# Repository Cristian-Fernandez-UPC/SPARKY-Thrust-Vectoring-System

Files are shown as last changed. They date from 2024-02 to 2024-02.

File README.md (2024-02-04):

# SPARKY Thrust Vectoring System
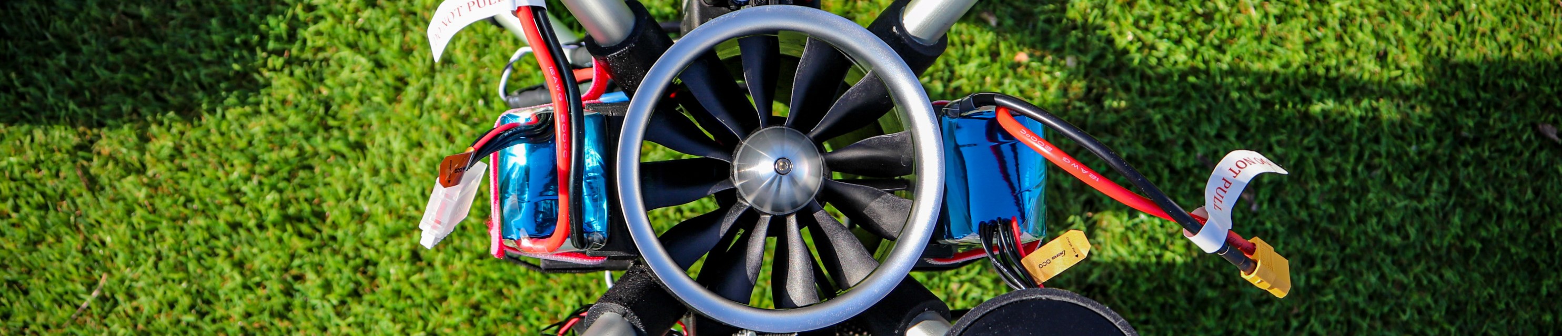
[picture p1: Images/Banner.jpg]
Banner

### Development and manufacturing of a Thrust Vectoring System for reusable rocket dynamics research - Final Bachelor's Thesis

Author: Cristian Fernandez Dominguez

Advisors: Pablo Royo Chic & Ramon Casanella Alonso

Bachelor’s degree in Aerospace Systems Engineering

Castelldefels School of Telecommunications and Aerospace Engineering

## :small_orange_diamond: Introduction
Nowadays, the space industry is experiencing exponential growth, fueled by private companies and the conception of new and ambitious challenges. In recent years, the cost of reaching space has been drastically reduced, and to a certain extent, reusable rockets are to blame for that cost reduction.

Unfortunately, and it has always been so, the space industry has always required a lot of resources and funding, and even with the drastic cost reduction with the incorporation of this new type of rockets, the development of technologies by students and researchers from universities around the world is still very difficult.

To address this problem, this thesis will attempt, by reducing the cost to a maximum, to develop a system where it can study the dynamics of reusable rockets and be able to develop technologies around them.

To do this, an unmanned aircraft system (UAS) will be designed from scratch with the main objective of imitating the behavior of this type of rocket while trying to reuse as many components already used by the university as possible, helping to reduce costs, and helping the sustainability of the project itself.

Through the different chapters of this work, it can be seen, from the conception of the initial requirements and selection of the components, to the 3D design and subsequent manufacturing of the system itself, which will be calibrated and tested in different test flights, taking advantage of the university's facilities.

## :small_orange_diamond: Media Overview
In this repository you can find all the files related of this final bachelor's thesis. Also the `Checklist` procedure and the `Connections Diagram` are in this repository. The files are organized as follows:

- [3D_Models](3D_Models) - This folder contains the `.stl` files for all components of Sparky. Utilizing these files, users with access to a suitable 3D printer can fabricate the individual parts and assemble them to create a functional UAS with VTOL capabilities.

- [3D_Sparky_Designs](3D_Sparky_Designs) - This folder gives access to the SolidWorks files of the different versions of Sparky and additionally to the Gimbal that works to calibrate the PIDs.

- [DataLogs](DataLogs) - This folder contains all the DataLogs in a `.bin` format of the different Flight Tests.

- [Images](Images) - Some cool images.

- [Parameters](Parameters) - This folder contains the different parameters used in the real flight tests in `.param` files.

In addition, a **YouTube channel** has been created to be able to upload the different videos of the test flights and a trailer that encompasses the entire project itself. The channel is [@CristianFernandezUPC](https://www.youtube.com/@CristianFernandezUPC/featured). 

The uploaded videos are:

- [Sparky Trailer](https://www.youtube.com/watch?v=5irSOpZRAP4)
- [Flight Test 1](https://www.youtube.com/watch?v=05G50puAUSE)
- [Flight Test 2](https://www.youtube.com/watch?v=WWrm3nAGPkM&t=1s)

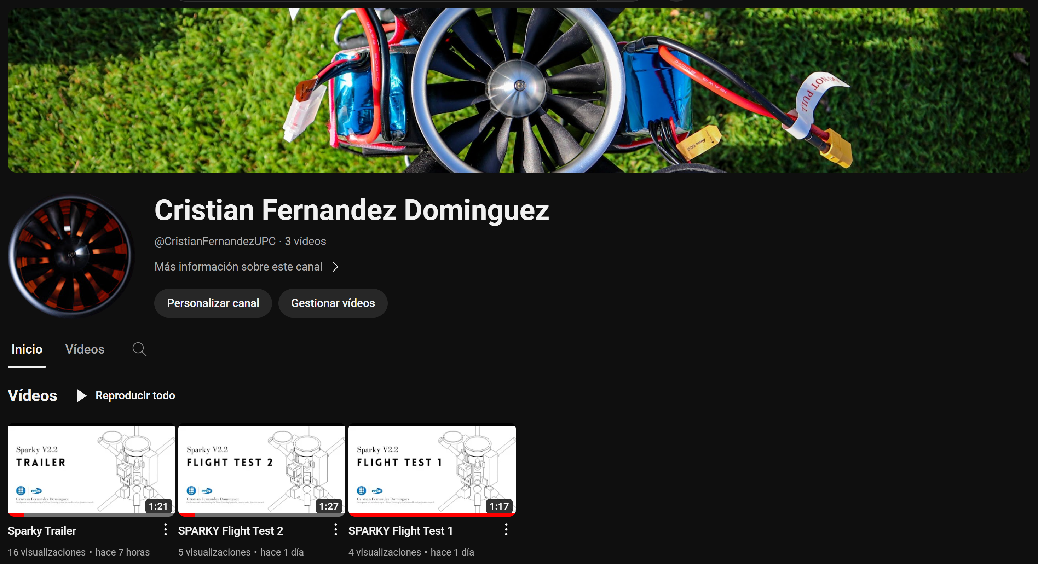
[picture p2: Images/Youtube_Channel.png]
ImgYoutube


## :small_orange_diamond: Components

- [Mini Set The Cube Orange+](https://rc-innovations.es/shop/pixhawk-2-1-mini-set-the-cube-orange-plus#attr=8269)

- [FrSky Taranis X9D PLUS](https://rc-innovations.es/shop/frsky-taranis-x9d-plus-se-2019-access-2-4ghz-carbono#attr=7182)

- [Here 3 + GPS Module](https://rc-innovations.es/shop/here-3-plus-modulo-gps-gnss-m8p-2-pixhawk-2-istand?search=here+3#attr=7478)

- [Gens ACE LiPo Battery 2500mAh (x2)](https://rc-innovations.es/shop/gens-ace-6s-22-2v-2500mah-80c-bateria-lipo?page=3&category=356#attr=8748,8749,8747)

- [KingMax Digital Servo (x4)](https://rc-innovations.es/shop/kingmax-km5514mdhv-20mm-59g-13kg-digital-metalico-coreless#attr=8001,7999,8000,8002)

- [HSD Jets EDF 90mm Brushless Motor](https://rc-innovations.es/shop/a58010000j-hsd-jets-s-edf-90mm-brushless-motor-10579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)

- [Hobbywing ESC 110A OPTO](https://rc-innovations.es/shop/esc-hobbywing-flyfun-hv-110a-v5-OPTO#attr=)

- [Holybro Telemetry Module V3](https://rc-innovations.es/shop/holybro-modulos-telemetria-sik-v3-433mhz-500mw?search=holybro+v3#attr=8351)

- [3DJake White Matte PLA 1000g (x2)](https://www.3djake.es/3djake/ecopla-mate-blanco)

- [Holybro PM02 V3 Power Module](https://rc-innovations.es/shop/modulo-alimentacion-pmu-holybro-pm02-v3-original-sensor-consumo-pmu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)

- [20mm Bearings](https://www.amazon.es/dp/B09VZGCW9H?ref=ppx_pop_dt_b_product_details&th=1)

- [Montana Paint Primer Plastics](https://www.amazon.es/dp/B0826FCM71?psc=1&ref=ppx_pop_dt_b_product_details)

- [Hobbywing UBEC 3A](https://rc-innovations.es/shop/Hobbywing-ubec-3a?search=ubec#attr=)

- [Anodized aluminum tube Ø16mm (1m) (x2)](https://www.fesmes.com/es/perfiles-de-aluminio/295205005-tubo-redondo-aluminio-anodizado-plata-8013237011109.html)

- [Montana Matte Black Paint](https://www.amazon.es/dp/B008UGFJU2?psc=1&ref=ppx_pop_dt_b_product_details)

- [Anodized Aluminum Square Tube 20mm x 20mm (1m)](https://www.fesmes.com/es/perfiles-de-aluminio/295204000-tubo-cuadrado-aluminio-anodizado-plata-8013237011925.html)

- [Anodized aluminum tube Ø20mm (1m)](https://www.fesmes.com/es/perfiles-de-aluminio/295205005-tubo-redondo-aluminio-anodizado-plata-8013237011109.html)

- [XT30 Connector (pair) (x3)](https://rc-innovations.es/shop/Amass-conector-xt30-pareja?search=xt30#attr=)

- [EC5 Connector (pair)](https://rc-innovations.es/shop/Hobbywing-ubec-3a?search=ubec#attr=)

## :small_orange_diamond: Project Images

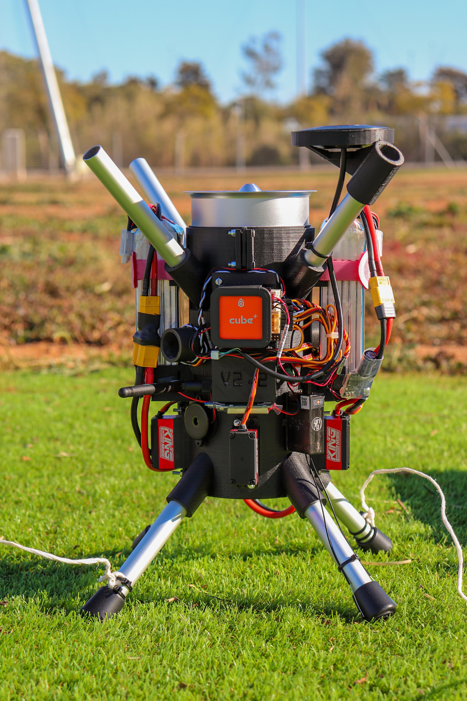
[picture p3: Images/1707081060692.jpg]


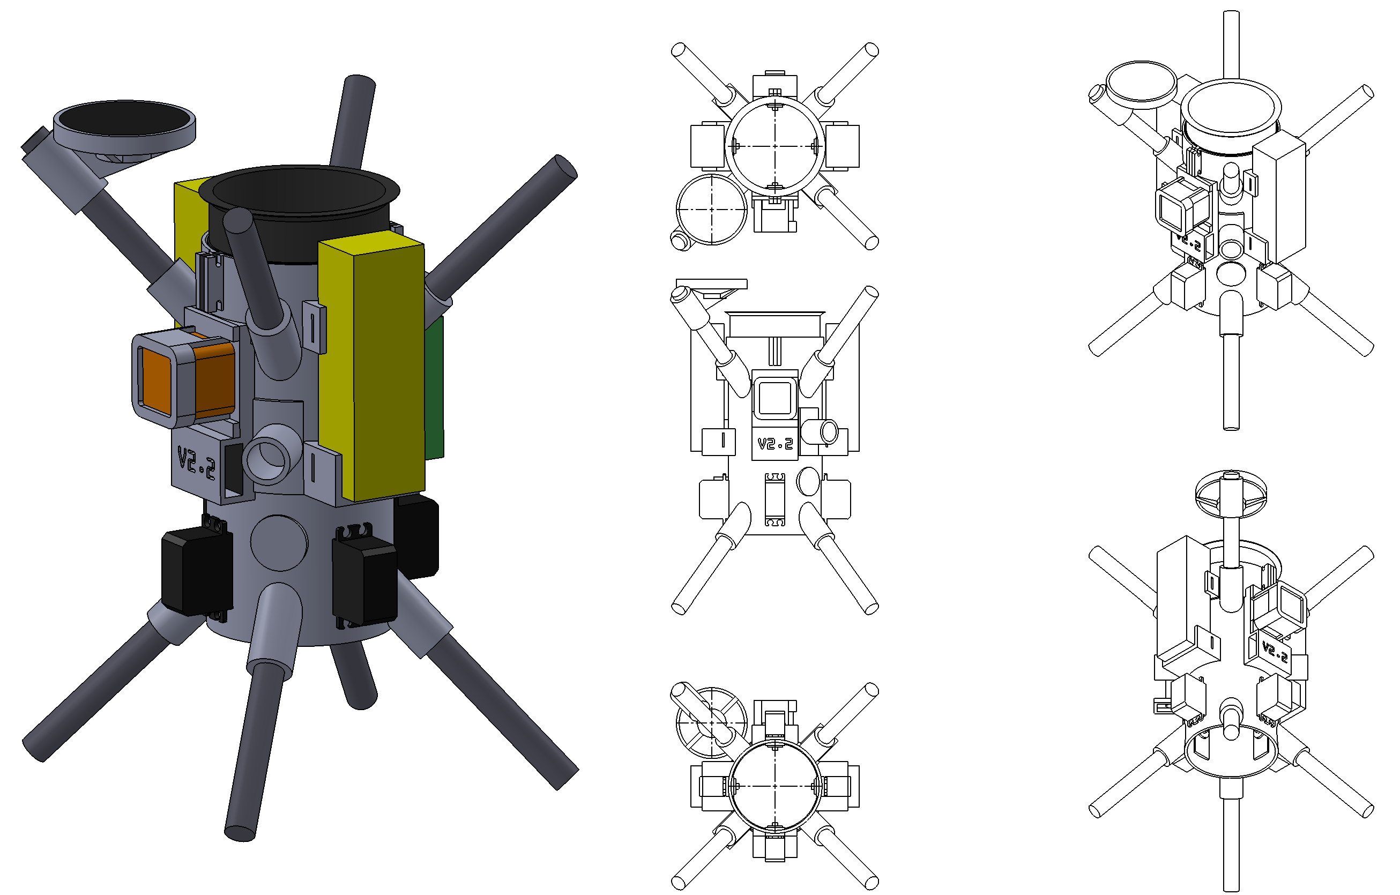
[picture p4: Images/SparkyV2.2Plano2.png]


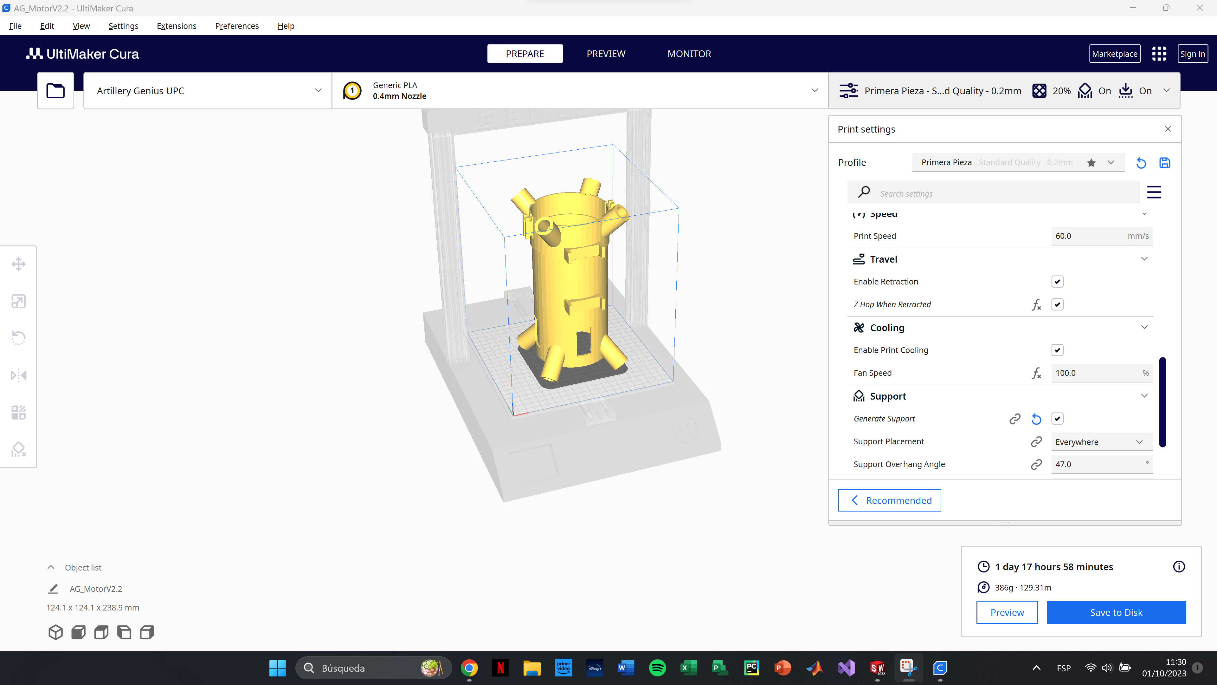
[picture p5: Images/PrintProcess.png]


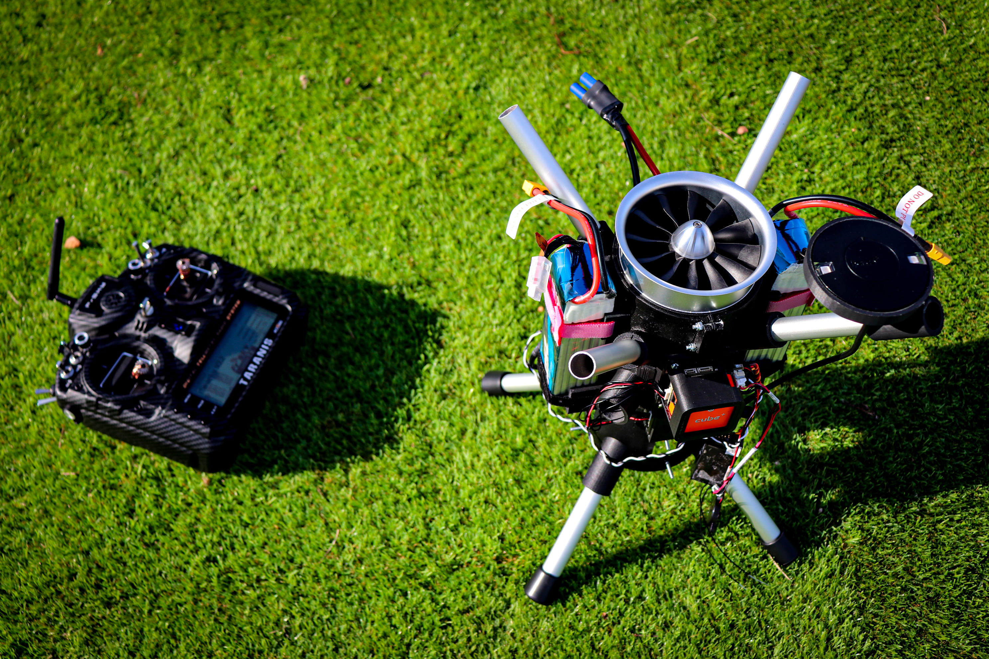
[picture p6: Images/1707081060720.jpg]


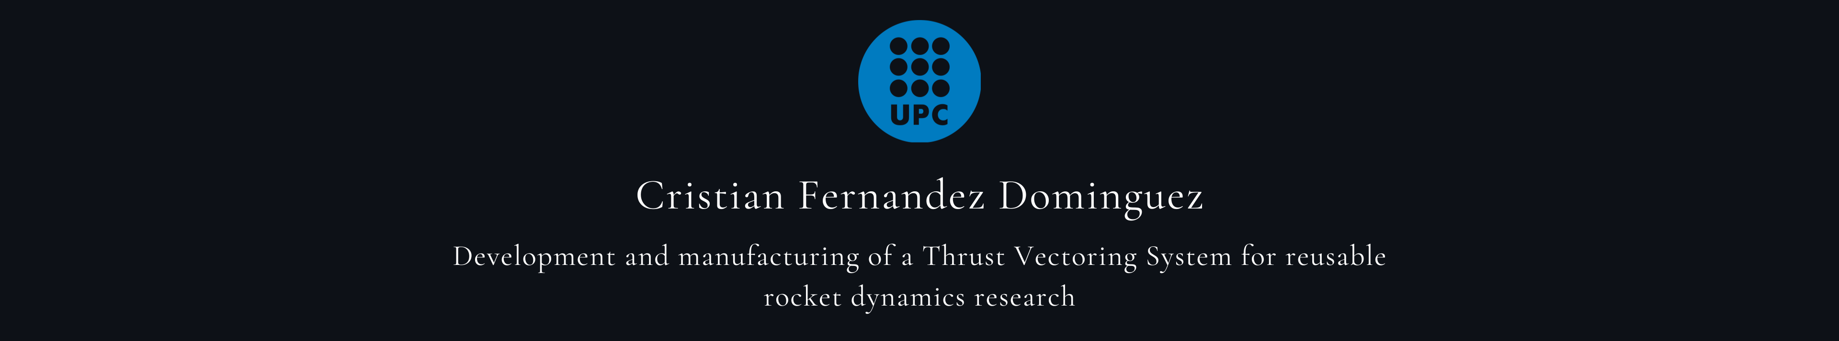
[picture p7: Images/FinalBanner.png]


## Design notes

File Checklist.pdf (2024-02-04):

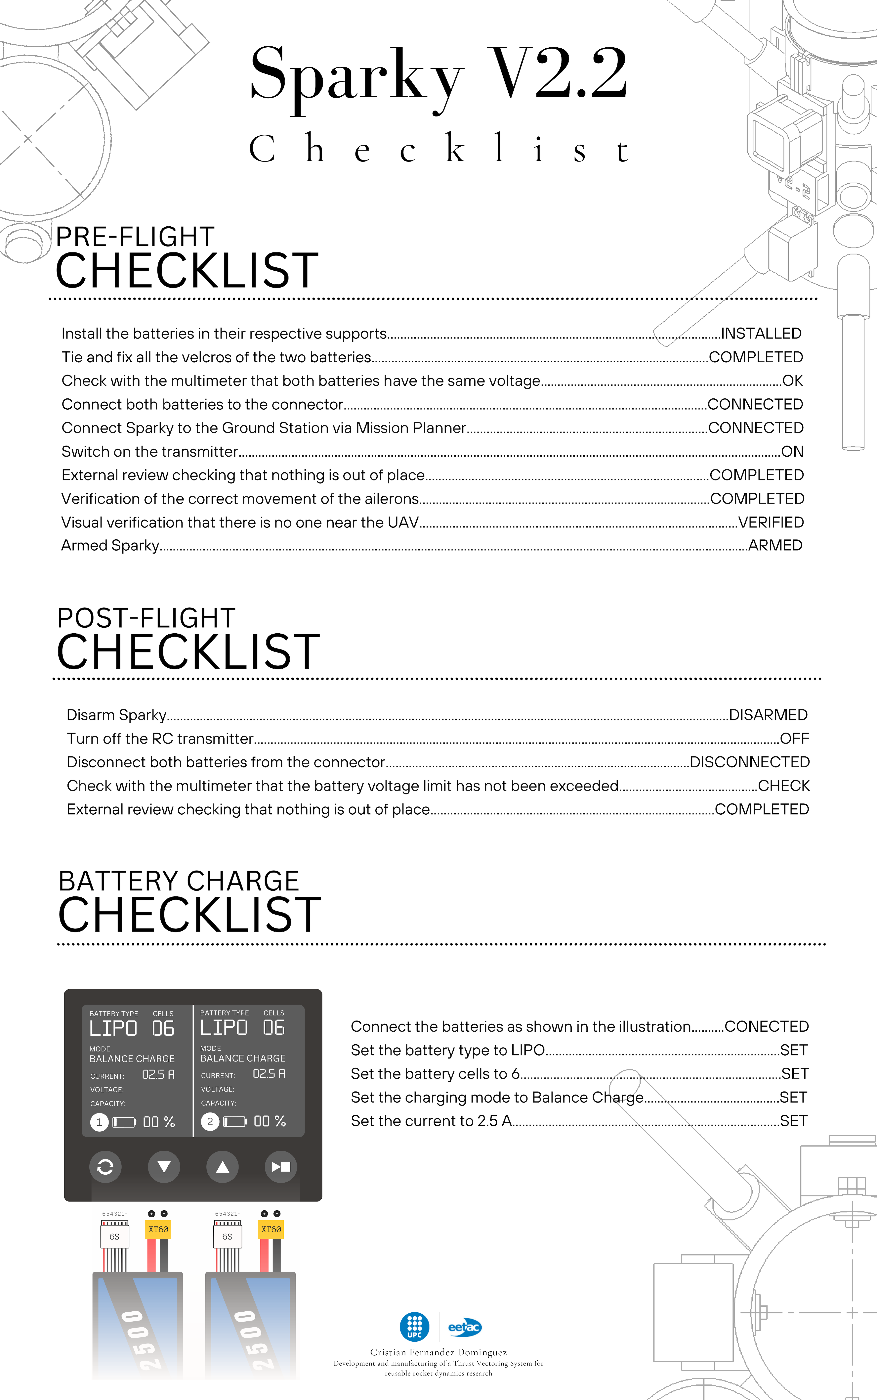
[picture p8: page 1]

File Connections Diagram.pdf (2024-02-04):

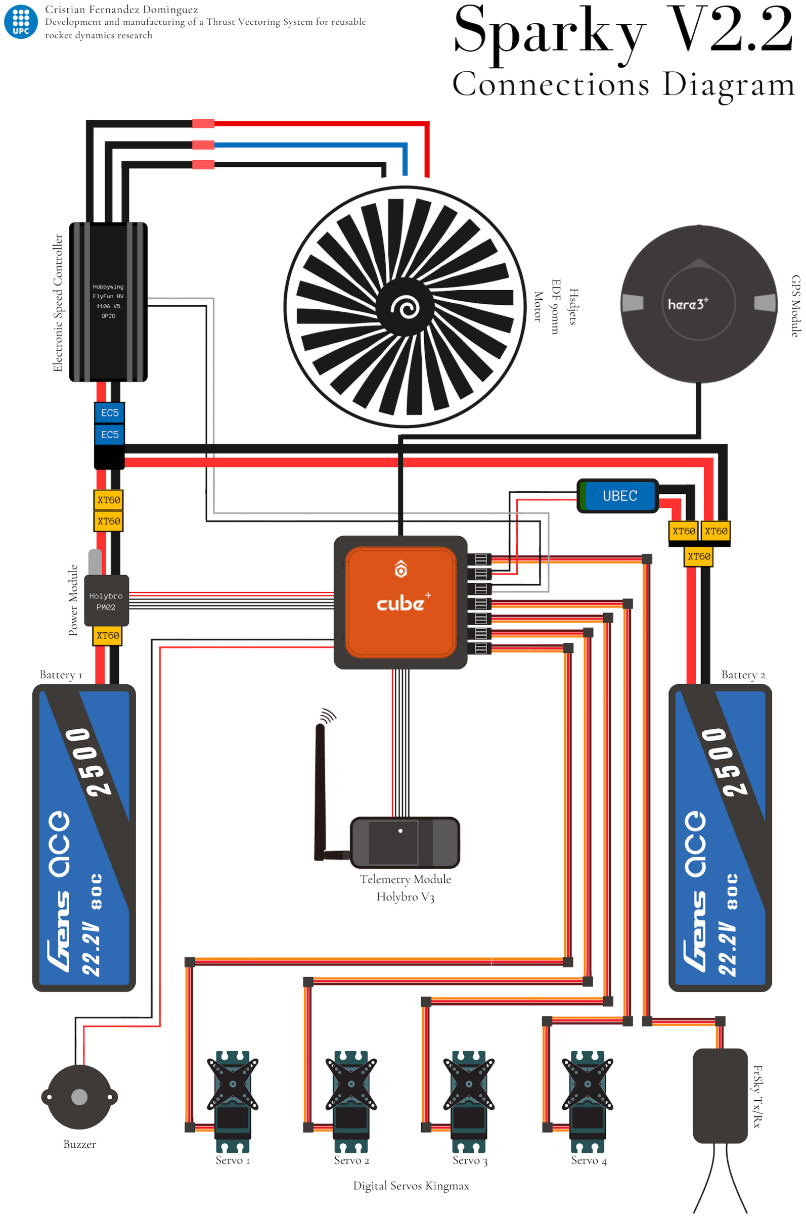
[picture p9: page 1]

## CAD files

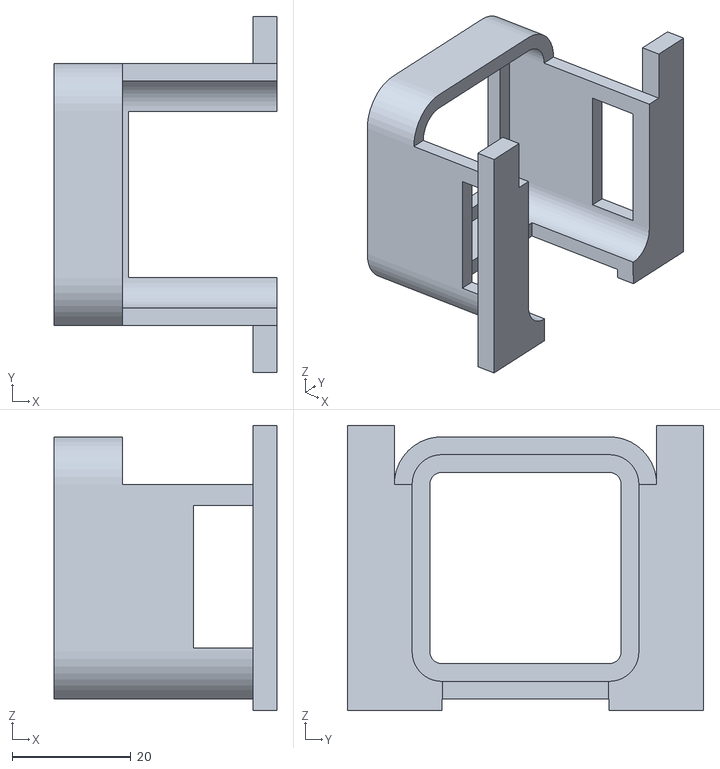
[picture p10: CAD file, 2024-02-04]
3D_Models/Cube 1_Support.STL
37.5 x 60.0 x 48.0

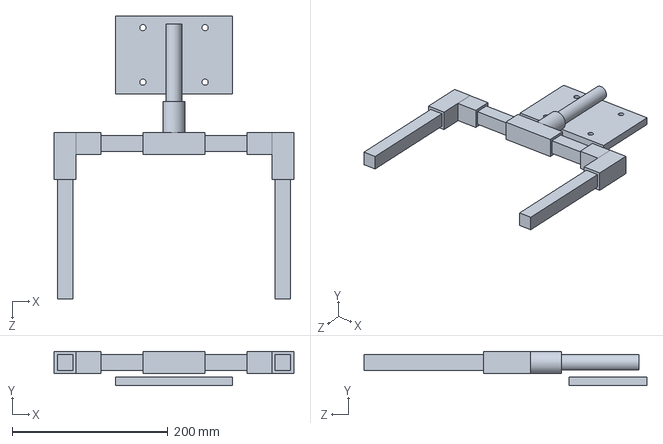
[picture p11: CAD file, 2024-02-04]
3D_Sparky_Designs/Gimbal_Support.SLDPRT
308.0 x 44.2 x 363.8 mm

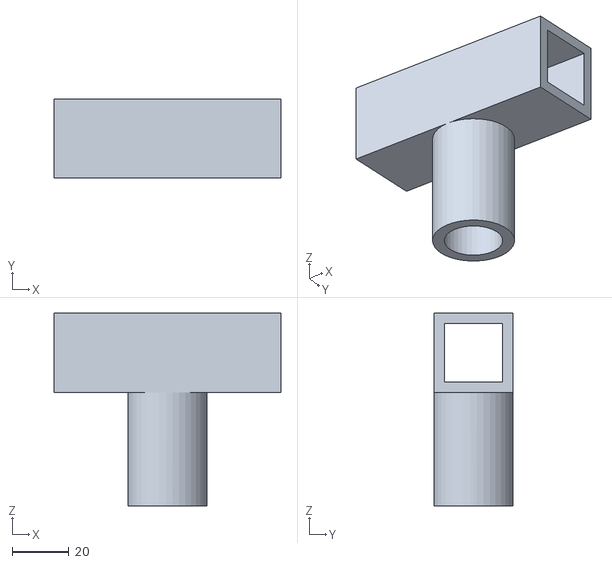
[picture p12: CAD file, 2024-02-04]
3D_Models/Gimbal_1_V2_Support.STL
80.0 x 28.0 x 68.0

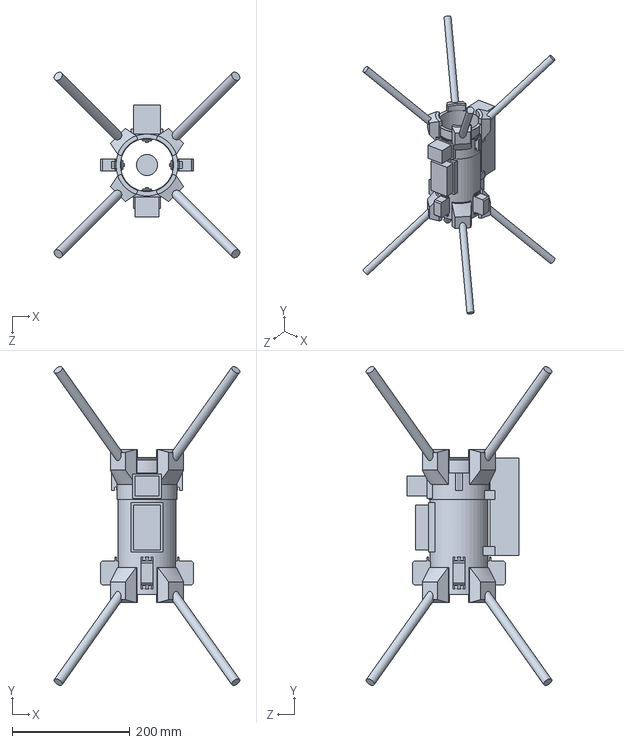
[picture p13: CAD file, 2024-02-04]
3D_Sparky_Designs/Sparky_V2.SLDPRT
315.1 x 541.1 x 315.1 mm

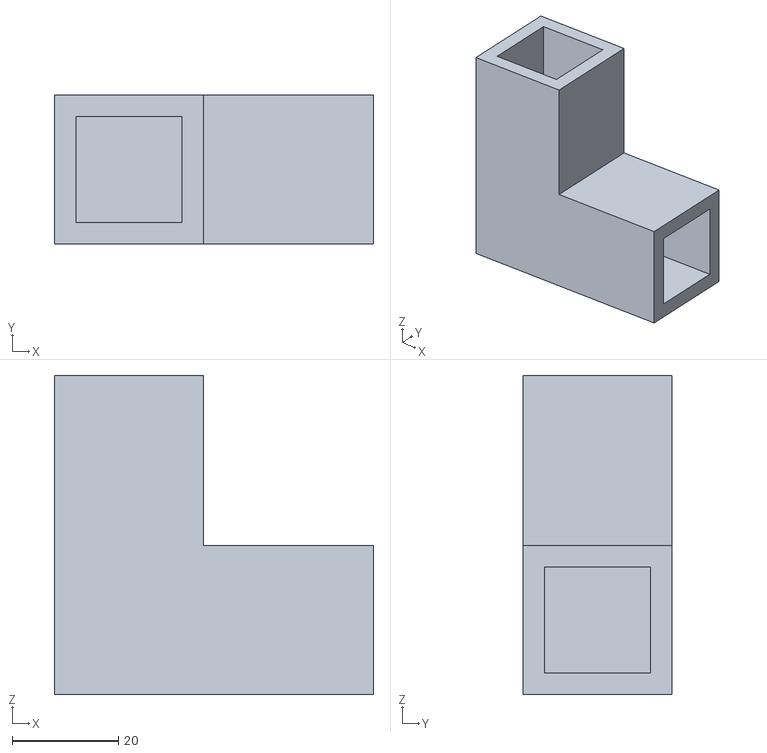
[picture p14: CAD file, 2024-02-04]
3D_Models/Gimbal_2_Support.STL
60.0 x 28.0 x 60.0

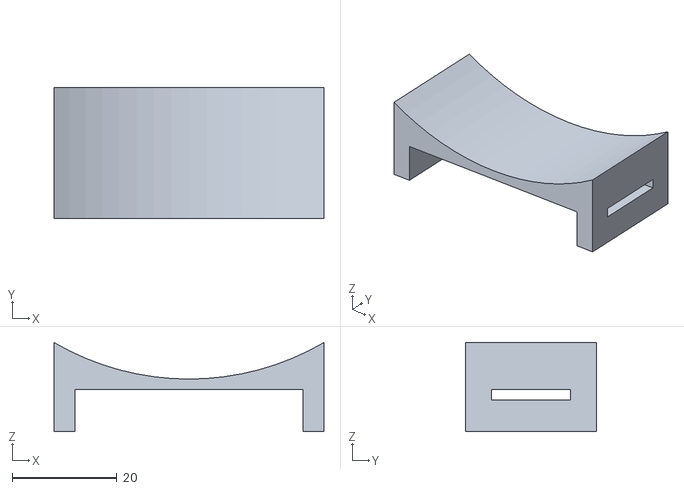
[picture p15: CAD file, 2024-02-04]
3D_Models/BAT_1_Support.STL
51.5 x 25.0 x 17.0

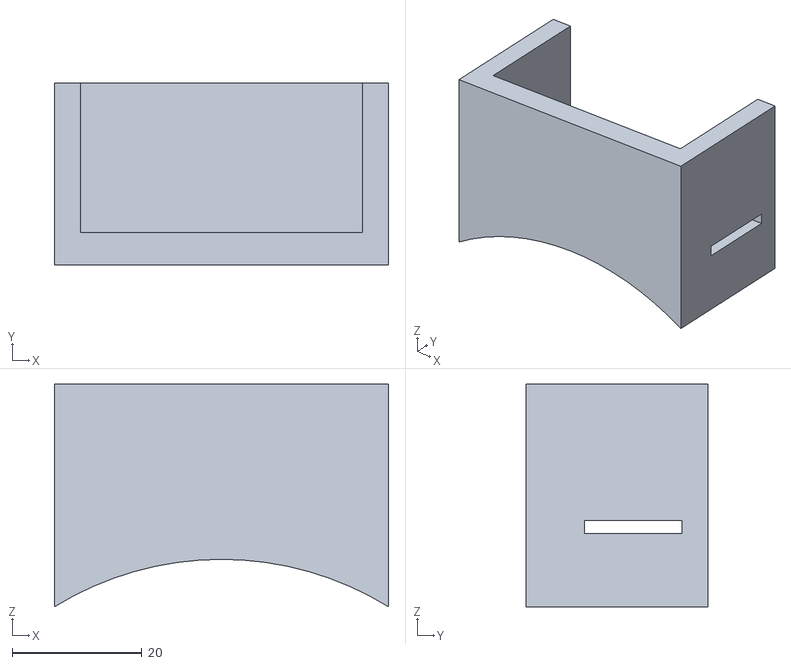
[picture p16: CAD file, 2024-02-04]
3D_Models/BAT_2_Support.STL
51.5 x 28.0 x 34.3

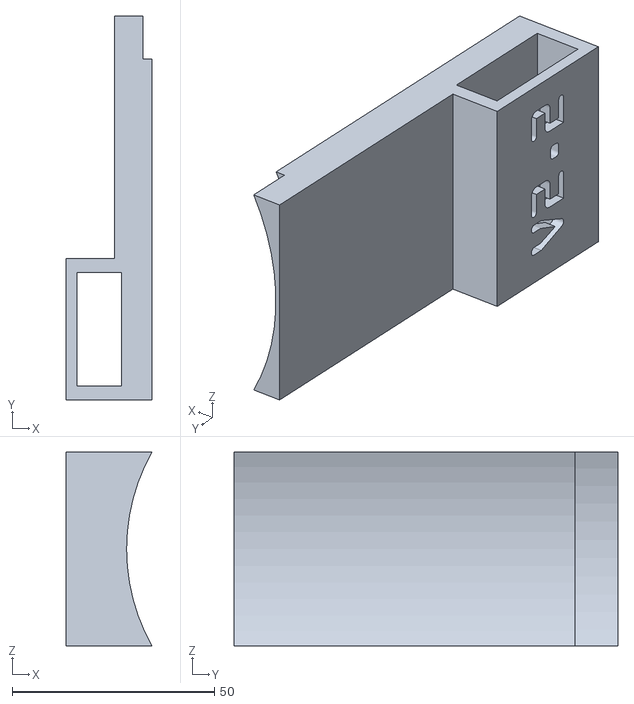
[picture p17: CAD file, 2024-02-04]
3D_Models/Cube 2_Support.STL
21.3 x 95.0 x 48.0

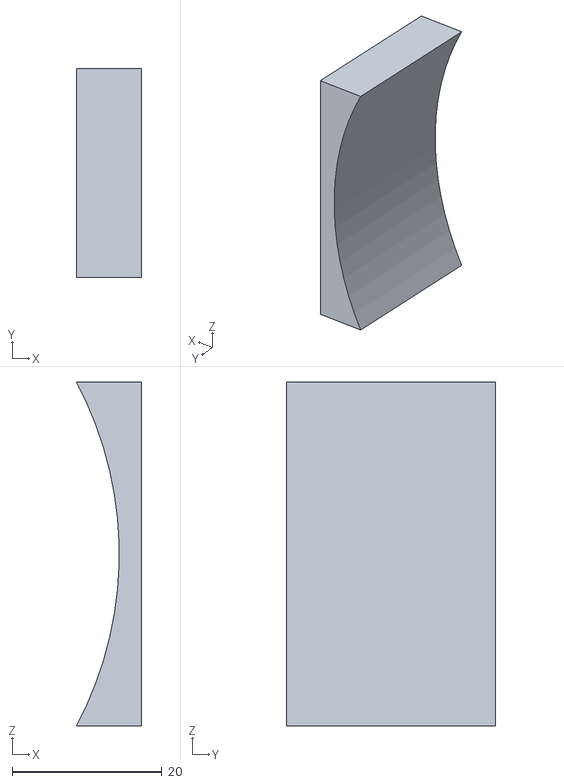
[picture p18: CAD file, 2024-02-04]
3D_Models/ESC_1_Support.STL
8.73 x 28.0 x 46.0

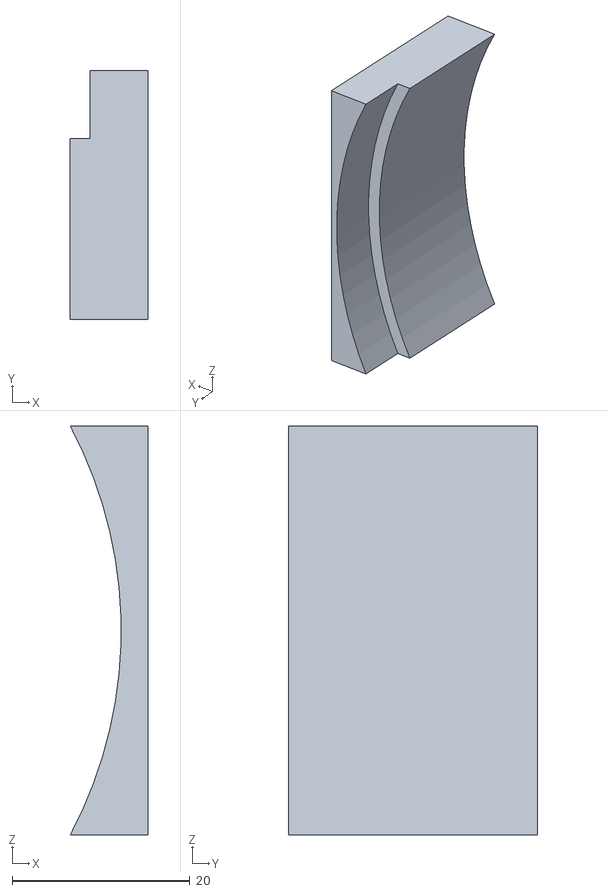
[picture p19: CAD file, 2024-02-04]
3D_Models/ESC_2_Support.STL
8.73 x 28.0 x 46.0

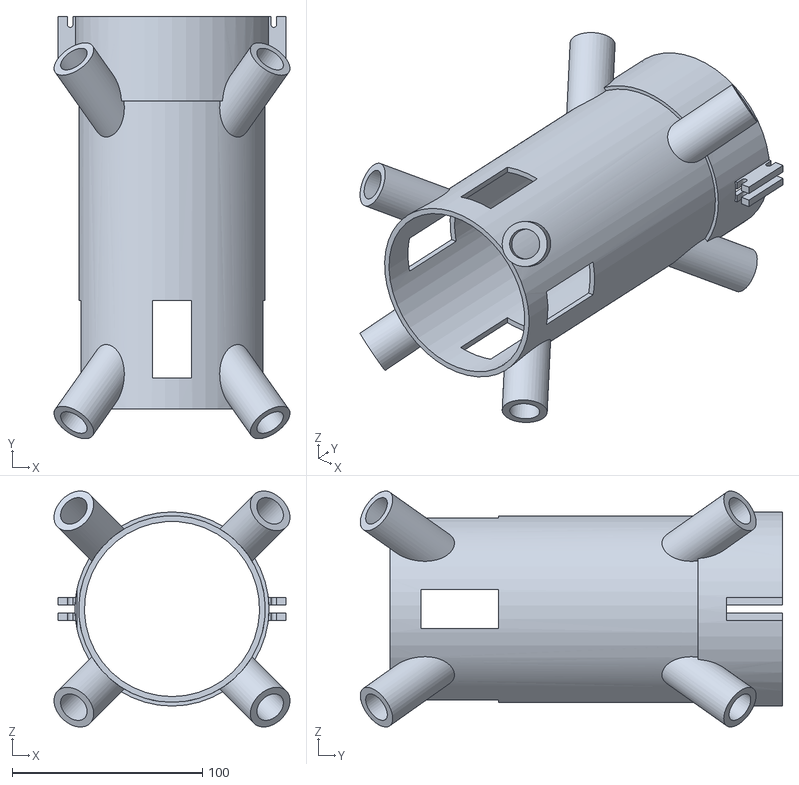
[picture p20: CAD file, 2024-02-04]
3D_Models/Sparky_V.2.2_Structure.STL
124.0 x 221.9 x 124.0

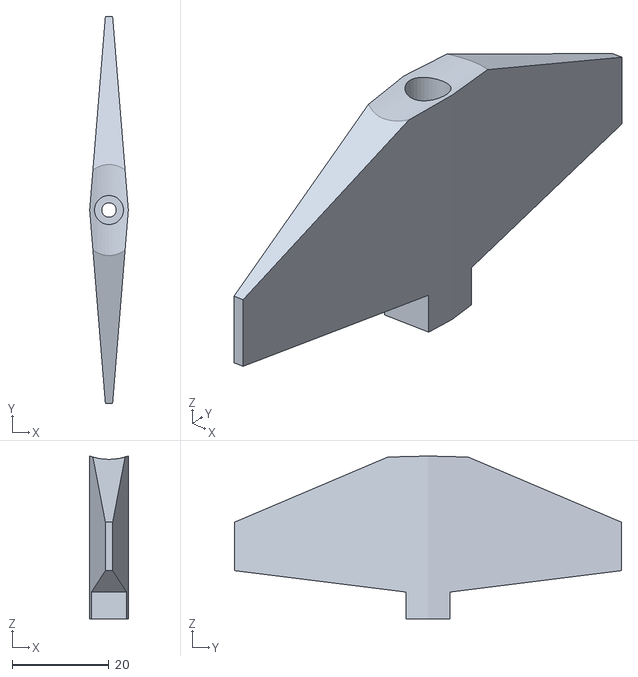
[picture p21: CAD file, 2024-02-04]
3D_Models/25T_Aileron_V2.2.STL
8.00 x 80.0 x 33.7

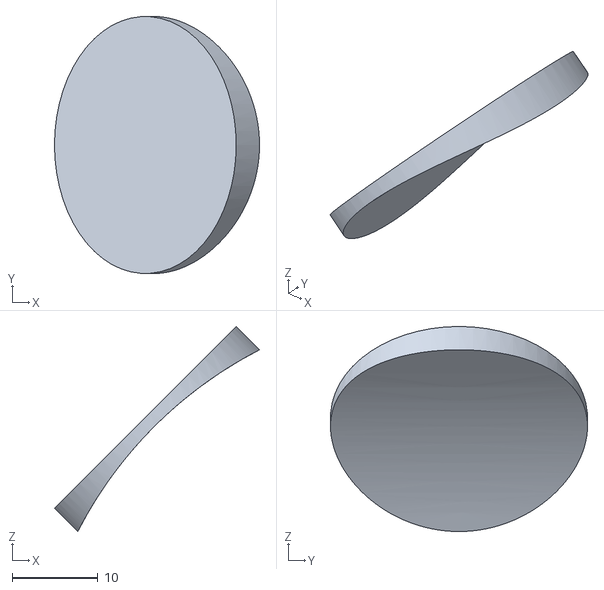
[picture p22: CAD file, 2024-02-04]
3D_Models/Buzzer_Support.STL
23.9 x 30.0 x 23.9

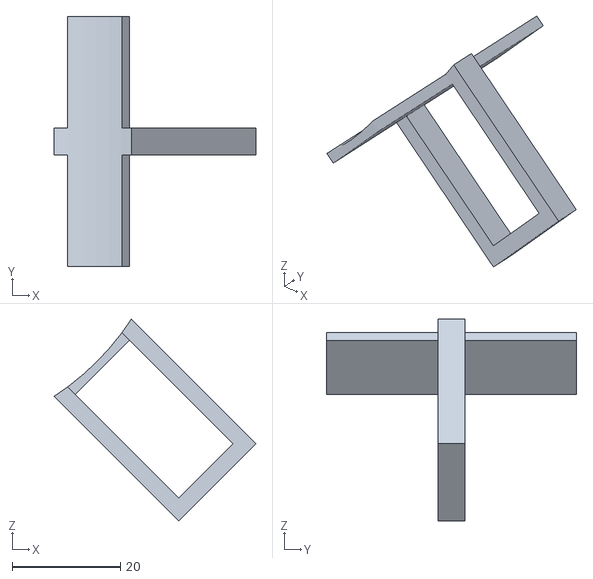
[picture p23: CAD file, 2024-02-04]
3D_Models/Radio_Support.STL
37.3 x 46.2 x 37.3

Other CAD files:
3D_Models/GPS_Support.STL
3D_Models/Base_Gimbal.STL
3D_Models/Gimbal_3_Support.STL

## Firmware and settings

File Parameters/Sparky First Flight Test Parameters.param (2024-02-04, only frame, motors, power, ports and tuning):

ATC_ANG_LIM_TC,1
ATC_ANG_PIT_P,8
ATC_ANG_RLL_P,8
ATC_ANG_YAW_P,4.5
ATC_ANGLE_BOOST,1
ATC_RAT_PIT_D,0
ATC_RAT_PIT_FF,0
ATC_RAT_PIT_FLTD,100
ATC_RAT_PIT_FLTE,0
ATC_RAT_PIT_FLTT,100
ATC_RAT_PIT_I,0.01
ATC_RAT_PIT_IMAX,0
ATC_RAT_PIT_P,1
ATC_RAT_PIT_SMAX,0
ATC_RAT_RLL_D,0
ATC_RAT_RLL_FF,0
ATC_RAT_RLL_FLTD,100
ATC_RAT_RLL_FLTE,0
ATC_RAT_RLL_FLTT,100
ATC_RAT_RLL_I,0.01
ATC_RAT_RLL_IMAX,0
ATC_RAT_RLL_P,1
ATC_RAT_RLL_SMAX,0
ATC_RAT_YAW_D,0
ATC_RAT_YAW_FF,0
ATC_RAT_YAW_FLTD,0
ATC_RAT_YAW_FLTE,2
ATC_RAT_YAW_FLTT,50.5
ATC_RAT_YAW_I,0.018
ATC_RAT_YAW_IMAX,0.02
ATC_RAT_YAW_P,0.18
ATC_RAT_YAW_SMAX,0
ATC_RATE_FF_ENAB,1
ATC_RATE_P_MAX,0
ATC_RATE_R_MAX,0
ATC_RATE_Y_MAX,0
BATT_MONITOR,0
BATT2_MONITOR,0
BATT3_MONITOR,0
BATT4_MONITOR,0
BATT5_MONITOR,0
BATT6_MONITOR,0
BATT7_MONITOR,0
BATT8_MONITOR,0
BATT9_MONITOR,0
FLTMODE_CH,8
FLTMODE1,0
FLTMODE2,5
FLTMODE3,0
FLTMODE4,5
FLTMODE5,0
FLTMODE6,6
FRAME_CLASS,8
FRAME_TYPE,1
INS_GYRO_FILTER,101
INS_HNTCH_ENABLE,0
MOT_BAT_CURR_MAX,0
MOT_BAT_CURR_TC,5
MOT_BAT_IDX,0
MOT_BAT_VOLT_MAX,151.2
MOT_BAT_VOLT_MIN,118.8
MOT_BOOST_SCALE,0
MOT_HOVER_LEARN,2
MOT_PWM_MAX,2000
MOT_PWM_MIN,1000
MOT_PWM_TYPE,0
MOT_SAFE_DISARM,0
MOT_SAFE_TIME,1
MOT_SLEW_DN_TIME,0
MOT_SLEW_UP_TIME,0
MOT_SPIN_ARM,0.1
MOT_SPIN_MAX,0.95
MOT_SPIN_MIN,0.15
MOT_SPOOL_TIME,0.5
MOT_THST_EXPO,0.5
MOT_THST_HOVER,0.2
MOT_YAW_HEADROOM,200
SERIAL0_BAUD,115
SERIAL0_PROTOCOL,2
SERIAL1_BAUD,57
SERIAL1_OPTIONS,0
SERIAL1_PROTOCOL,2
SERIAL2_BAUD,57
SERIAL2_OPTIONS,0
SERIAL2_PROTOCOL,2
SERIAL3_BAUD,38
SERIAL3_OPTIONS,0
SERIAL3_PROTOCOL,5
SERIAL4_BAUD,38
SERIAL4_OPTIONS,0
SERIAL4_PROTOCOL,5
SERIAL5_BAUD,57
SERIAL5_OPTIONS,0
SERIAL5_PROTOCOL,1
SERIAL6_BAUD,115200
SERIAL6_OPTIONS,0
SERIAL6_PROTOCOL,22
SERVO1_FUNCTION,33
SERVO1_MAX,1990
SERVO1_MIN,1390
SERVO1_REVERSED,0
SERVO1_TRIM,1690
SERVO2_FUNCTION,34
SERVO2_MAX,1800
SERVO2_MIN,1200
SERVO2_REVERSED,0
SERVO2_TRIM,1500
SERVO3_FUNCTION,35
SERVO3_MAX,1730
SERVO3_MIN,1130
SERVO3_REVERSED,0
SERVO3_TRIM,1430
SERVO4_FUNCTION,36
SERVO4_MAX,1510
SERVO4_MIN,910
SERVO4_REVERSED,0
SERVO4_TRIM,1210
SERVO5_FUNCTION,53
SERVO5_MAX,1900
SERVO5_MIN,1100
SERVO5_REVERSED,0
SERVO5_TRIM,1500
SERVO6_FUNCTION,38
SERVO6_MAX,1900
SERVO6_MIN,1100
SERVO6_REVERSED,0
SERVO6_TRIM,1500
SERVO7_FUNCTION,0
SERVO7_MAX,1900
SERVO7_MIN,1100
SERVO7_REVERSED,0
SERVO7_TRIM,1500
SERVO8_FUNCTION,0
SERVO8_MAX,1900
SERVO8_MIN,1100
SERVO8_REVERSED,0
SERVO8_TRIM,1500
SERVO9_FUNCTION,0
SERVO9_MAX,1900
SERVO9_MIN,1100
SERVO9_REVERSED,0
SERVO9_TRIM,1500

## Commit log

2024-02-04 Rename Cube 1_Support.STL to 3D_Models/Cube 1_Support.STL
    [Cube 1_Support.STL]
2024-02-04 Rename Cube 2_Support.STL to 3D_Models/Cube 2_Support.STL
    [Cube 2_Support.STL]
2024-02-04 Update and rename Sparky First Flight Test Parameters.param to Parameters/Sparky First Flight Test Parameters.param
    [Sparky First Flight Test Parameters.param]
2024-02-04 Update and rename Sparky Second Flight Test Parameters.param to Parameters/Sparky Second Flight Test Parameters.param
    [Sparky Second Flight Test Parameters.param]
2024-02-04 Rename Captura de pantalla 2023-10-01 113053.png to PrintProcess.png
